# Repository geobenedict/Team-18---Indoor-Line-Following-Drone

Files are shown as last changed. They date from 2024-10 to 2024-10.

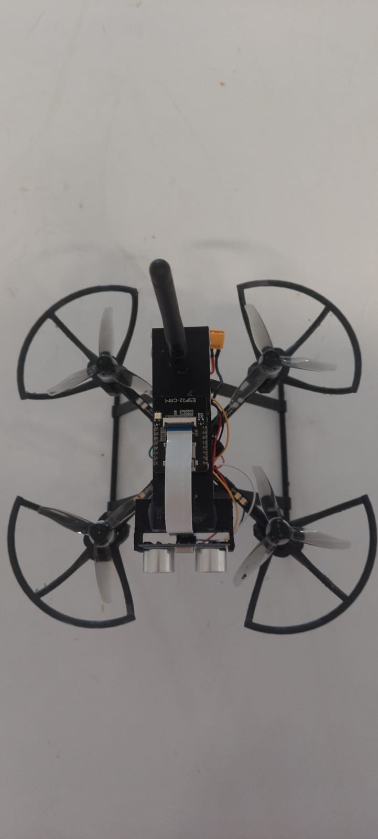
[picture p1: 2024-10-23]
Hardware-diagrams/Prototype Top View.jpeg

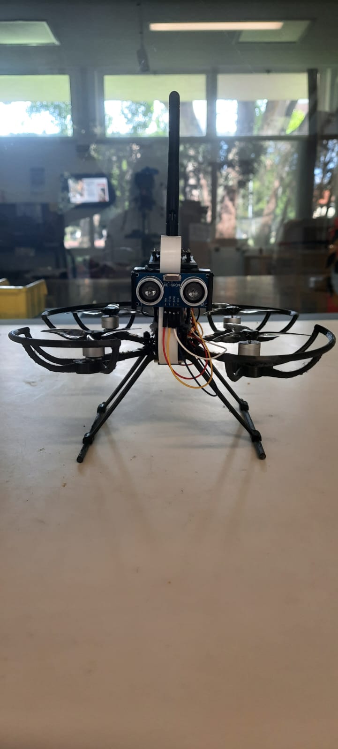
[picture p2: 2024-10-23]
Hardware-diagrams/Prototype Front View.jpeg

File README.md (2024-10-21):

# Team-18---Indoor-Line-Following-Drone

Welcome to the official repository for **Team 18's Indoor Line Following Drone Project**. This repository contains all the necessary files, including code, design deliverables, bills of materials, 3D print designs, and the design validation tests and results. The aim of this project is to develop a drone capable of autonomously following a predefined path indoors using a line-following navigation system.

## Project Overview

This project focuses on creating a lightweight, agile drone designed for indoor environments, equipped with a line-following system using the **ESP32-CAM** module and **OpenCV** for real-time image processing. The system captures live video, processes it to detect a line, and sends commands to control the drone's movements, ensuring it follows a predefined path.

### Key Features:
- Real-time video streaming via the **ESP32-CAM**.
- Line detection and navigation using **OpenCV**.
- Agile indoor navigation on the **Darwin FPV BabyApe Pro V2** platform.
- Design validation tests for line detection, curve navigation, and T-junction stopping.

## Repository Structure
📂 Team-18-Indoor-Line-Following-Drone ├── 📂 3d-Designs/ # 3D print designs for drone components ├── 📂 BoM/ # Bill of Materials (BoM) and expenses ├── 📂 Codes/ # Contains all the code for the ESP32-CAM and OpenCV integration  ├── 📂 Validation-tests/ # Design validation tests and results ├── 📂 Hardware-diagrams/ # Diagrams related to drone hardware and setup ├── 📄 README.md # Project overview and repository guide

## Getting Started

### Prerequisites

- **ESP32-CAM**: Ensure that the ESP32-CAM is set up using the Arduino IDE to act as an Access Point and stream video.
- **OpenCV**: Install   Pycharm to process the video feed and control the drone.
- **Arduino IDE**: Program the ESP32-CAM using the provided `.ino` code files in the `/Codes` folder.

### Installation

1. Clone the repository:
git clone https://github.com/geobenedict/Team-18---Indoor-Line-Following-Drone.git
2. Follow the instructions in the **/Codes** folder to upload the ESP32-CAM code via the Arduino IDE.
3. Use the Python code in the `/Codes` folder to set up the OpenCV environment for processing the video feed.

### Running the Project

1. Connect the **ESP32-CAM** to the drone and power it up.
2. Run the Python script from the `/Codes` folder to process the video stream and control the drone.
3. Validate the drone’s line-following performance by running the tests outlined in the **/Validation-tests** folder.

## Design Deliverables

- **3D Designs**: The `/3d-Designs` folder contains all the 3D print designs for custom drone components.
- **Bills of Materials**: All parts used in the project, along with their costs, are listed in the `/BoM` folder.
- **Hardware Diagrams**: Detailed hardware setup and wiring diagrams are located in the `/hardware-diagrams` folder.
- **Validation Tests and Results**: Test cases for straight-line, curve, and T-junction detection, along with their results, are found in the `/Validation-tests` folder.

## Design Validation

The design validation process included multiple tests, such as:
- **Straight Line Detection Test**: Ensures the drone follows a straight path.
- **Curved Path Detection Test**: Validates the drone’s ability to follow a curved line.
- **T-Junction Detection Test**: Confirms that the drone can detect a T-junction and stop as required.
- **Battery Drain Test**: Validates the efficiency of the battery's charge and discharge cycles by monitoring voltage levels, runtime, and overall power consumption under operational conditions.

Test results and detailed analysis are provided in the **/Validation-tests** folder.

**Team 18 - Indoor Line Following Drone Project**

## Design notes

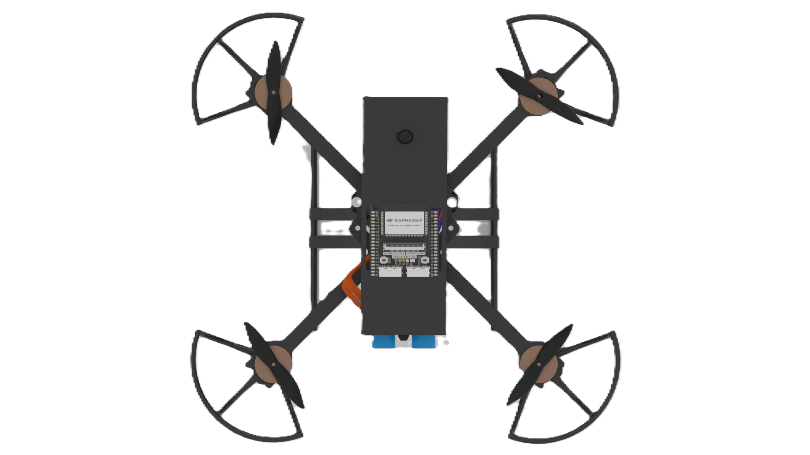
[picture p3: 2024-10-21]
Hardware-diagrams/Drone_top view.png

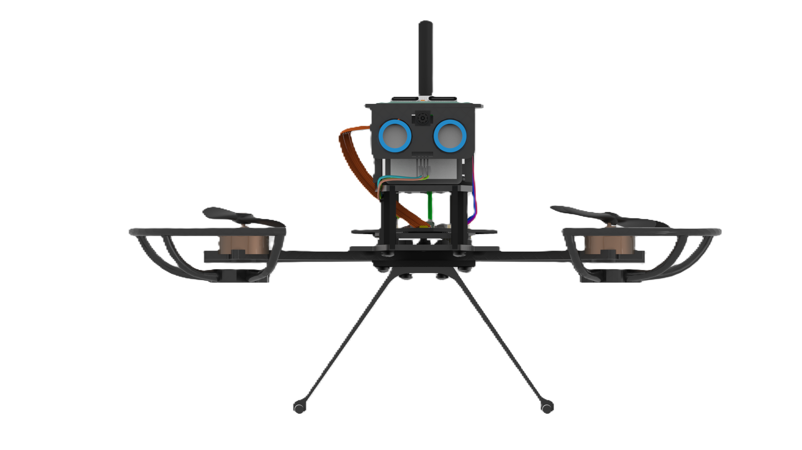
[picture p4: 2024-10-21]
Hardware-diagrams/drone front view.png

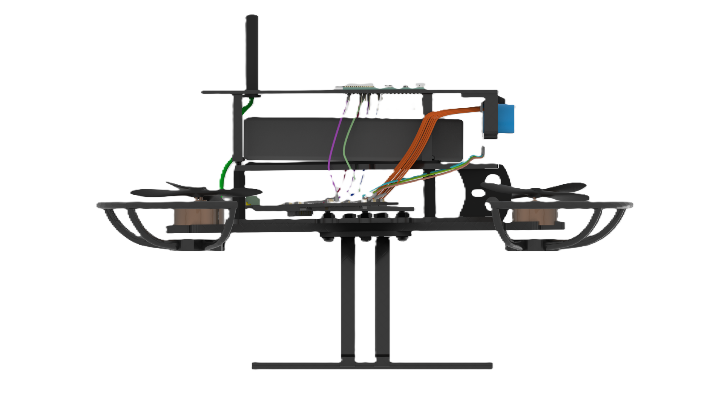
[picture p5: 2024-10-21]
Hardware-diagrams/Drone_side.png

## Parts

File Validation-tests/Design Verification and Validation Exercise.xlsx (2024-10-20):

Indoor Line Tracking Drone
ID | Requirement description | Test | Passed | Learnings
RQ1 | Follow the predefined path | Line Following Test: Use the ESP32-CAM to follow a predefined path (straight, curved, and T-junction) and verify correct navigation through image processing. Measure command accuracy for lateral and rotational adjustments. | Yes | The requirement was correctly tested, and the ESP32-CAM successfully followed the predefined path. However, variations in lighting conditions slightly impacted the accuracy of line detection. In future iterations, optimizing threshold values for varying lighting could enhance performance.
RQ2 | Battery Specifications | Battery Drain Test: Discharge the drone's battery fully while monitoring voltage levels and time taken. Record the total run time and compare against specifications. Perform a charging test to evaluate recharge time. | Yes | The battery drain and recharge process were successful, and no issues were observed with the battery specifications. Ensuring efficient power management and considering faster charging methods could further optimize drone operations.
RQ3 | Obstacle Detection | Sensor Obstacle Detection Test: Place obstacles at varying distances (20-50cm) and measure the response time of the ultrasonic sensor in triggering the hover or stop functions. Analyze detection accuracy and range. | Yes | The system successfully detected obstacles within 30cm. The sensor worked best within shorter distances, and future improvements could focus on increasing the detection range or adding more sensitive sensors for enhanced accuracy.
RQ4 | Project Deliverables | Documentation Review: Conduct a thorough review of all required project deliverables including the Bill of Materials (BOM), schematics, safety reports, and final project reports to ensure compliance. | Yes | All deliverables, including BOM and safety reports, were thoroughly reviewed with no discrepancies found. The project documentation is up to date ensuring compliance with the deliverables outlined in the project brief.
RQ5 | Fail-Safe Mechanisms | Emergency Stop Test: Simulate communication loss for over 30 seconds. Test the response of the manual emergency stop switch implemented using the ESP32 shield and verify if the drone halts all operations as expected. | No | The lack of integration between the hardware and software prevented full functionality. The system was not able to trigger the emergency stop during testing, and we could not test its behavior in a flight scenario. Integration challenges ultimately prevented a complete test of the fail-safe mechanism.
RQ6 | Safety Mechanisms - Propeller Shrouds | Motor and Propeller Guard Test: Run the motors at full speed with the propeller shrouds attached to verify that they effectively protect against damage and ensure safe operation in enclosed spaces. | Yes | The propeller guards performed as expected, protecting the motors and blades from potential damage. The design of the guards is effective for indoor navigation, but failed in testing with the drone in operation
RQ7 | Hovering and Stability | Drift Tolerance Test: Use the gyroscope and accelerometer to stabilize the drone in place. Measure the drift over a fixed duration while hovering and compare against drift tolerance limits (10cm drift allowed). | No | Stability was not fully tested due to the lack of software-hardware integration. Further testing will be needed once the drone can fly to ensure it remains within allowable drift limits. The stability features via sensors remain untested in a real-flight scenario.
RQ8 | Stable Altitude | Altitude Hold Test: Set the drone at various heights (1m, 1.5m, 2m) and assess the drone's ability to maintain stable altitude. Measure any fluctuations and calculate the stability at each height. | No | Stable altitude could not be tested as the drone was not operational. The flight controller and sensor integration are pending, which will be required for altitude testing once integration issues are resolved.
RQ9 | Open Source Software | Software Integration Test: Test the integration of the OpenCV libraries with the Arduino IDE for processing video feeds and executing commands. Ensure that the software correctly detects paths and sends commands to the drone. | Yes | Open-source libraries, including OpenCV and Arduino IDE, were successfully implemented, allowing for real-time video capture and processing. This was a cost-effective and flexible solution, reducing dependency on proprietary software and hardware platforms.
RQ10 | Budget Limit | BoM Review and Budget Test: Cross-check all components in the Bill of Materials (BoM) and ensure the total project cost does not exceed the $350 budget. Evaluate additional costs for any unforeseen expenses. | Yes | All components were purchased within the allocated budget of $350, with the current total reaching $300. The project remains within financial constraints, ensuring cost-efficiency.
RQ11 | Flight Range | Flight Duration and Range Test: Fully charge the drone's battery and run the drone to test the maximum flight range and duration. Measure the total distance covered on a full charge and ensure it meets the minimum range requirement. | No | Flight range could not be tested due to incomplete integration of the flight control system. This test will need to be conducted once the drone becomes operational to ensure that it meets the expected range requirements.
RQ12 | Collision Avoidance and Emergency Landing | Collision Avoidance Test: Simulate obstacles in the drone’s path. Test the ability of the system to detect obstacles using sensors and perform an emergency landing or hover. Record the time taken for the drone to stop or land. | No | Although the sensors were set up, collision avoidance and emergency landing could not be fully tested due to the incomplete integration of the flight system. These functionalities require proper sensor-drone interaction, which remains to be validated.
RQ13 | Product Quality | Durability Test: Monitor drone components (motors, sensors, propeller guards) over time by performing stress tests under normal and harsh conditions to assess long-term durability and consistent functionality. | Yes | Initial tests suggest that the components are durable and functional. However, extended monitoring is required to validate the long-term reliability of the hardware under normal operating conditions. The hardware components are currently performing as expected.
RQ14 | Communication via Base Station | Communication Stability Test: Set up the base station and ESP32 system. Test data transmission between the drone and base station over varying distances. Measure signal strength, latency, and data transfer consistency. | No | The communication between the drone and the base station could not be fully validated due to integration issues. Despite attempts to establish communication using the ESP32 module and antenna, reliable data transfer was not achieved. Future work will need to resolve these integration issues to ensure stable and continuous communication during operation.
RQ15 | Path Characteristics | Path Visibility Test: Assess the contrast and visibility of the path under different lighting conditions (e.g., bright and low light). Use the ESP32-CAM to verify the path’s detectability in various scenarios (floor type, path contrast). | Yes | Path detection worked well under various lighting conditions. The ESP32-CAM’s ability to distinguish the path was consistent, but fine-tuning is necessary to further improve contrast detection under extreme lighting differences.
RQ16 | Advanced Stabilizations | Betaflight Stabilization Test: Test the drone’s gyroscopes and accelerometers using Betaflight configurator. Verify if the drone stabilizes properly when external disturbances are applied during real-time flight simulation. | Yes | The gyroscopes and accelerometers were tested using the Betaflight configurator, and initial results indicated proper functionality for stabilization. However, full real-world testing could not be completed due to the lack of hardware-software integration, limiting the ability to verify stability during flight.
RQ17 | Battery Chargeability | Charging Test: Measure the time required to fully charge the battery using standard USB chargers. Record charging speed, temperature changes, and any indications of overcharging or overheating during the process. | Yes | The battery charging process worked effectively using standard USB chargers. Charging times were reasonable, and there were no issues with overheating or incorrect voltage. The charging process meets the project’s requirements and expectations.
RQ18 | Reliable Communication System | ESP32 Communication Range Test: Test the ESP32 module with external antennas to verify communication strength and reliability. Measure signal range and note any loss of connection or drop in data transmission as distance increases. | No | The integration of the ESP32 module with an external antenna was tested for enhancing communication range, but the system failed to provide reliable connectivity. Signal interference and loss of communication occurred at longer distances, highlighting the need for further refinement in antenna placement and communication protocols.
RQ19 | Size and Design Constraint | Dimensional Accuracy Test: Verify the dimensions of the drone to ensure it complies with size constraints for confined spaces. Ensure the frame and propeller guards allow safe navigation in tight spaces. | Yes | The drone’s size fits within the required constraints for indoor operations, ensuring it can navigate in tight and confined spaces. Further tests could confirm its suitability for environments with even more restricted dimensions.
RQ20 | Wi-Fi Coverage | Wi-Fi Strength Test: Use Wi-Fi signal strength tests to ensure data can be transmitted effectively over longer distances. Measure signal drop-off points and verify stability for continuous communication in a typical operational area. | Yes | Wi-Fi coverage was tested, and the signal strength was adequate for real-time data handling. The drone maintained stable communication over the tested distance, but further stress testing in environments with more interference would be beneficial for confirming robustness.

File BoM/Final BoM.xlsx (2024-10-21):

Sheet: BillOfMaterials
Bill Of Materials(BOM)
 | https://www.vertex42.com/ExcelTemplates/free-timesheet-template.html |  |  |  |  |  |  |  | © 2012-2019 Vertex42 LLC
 | Project Name : | Indoor Line Following Drone |  |  |  |  |  |  | Bill of Materials Template (https://www.vertex42.com/ExcelTemplates/bill-of-materials.html)
 | Assembly Revision : | 5 |  |  |  |  |  |  | ► More Inventory Templates (https://www.vertex42.com/ExcelTemplates/inventory.html)
 | Approval Date : |  |  |  |  |  |  |  | ► More Business Templates (https://www.vertex42.com/ExcelTemplates/business-templates.html)
 |  |  |  |  |  |  |  |  | ► More Spreadsheet Templates (https://www.vertex42.com/ExcelTemplates/)
 | Total Cost : | $349.27
Part # | Part Name | Description | Qty | Supplier | Unit Cost | Shipping charge | Tax | Total Cost
1 | Drone Kit | DarwinFPV BabyApe Pro V2 3 Inch Analog FPV Drone | 1 | FPV Faster | $145.87 |  | $14.59 | $160.46
2 | Battery | GAONENG GNB 720mAh 2S 100C 7.6V LiHV LiPo Battery Long Type XT30 [DG] | 1 | FPV Faster | $16.99 | $14.51 |  | $31.50
3 | Propeller | GEMFAN 3016 Hurricane Propeller Toothpick 3 Blade | 4 | FPV Faster | $3.99 |  |  | $3.99
4 | Battery Charger | MMOBIEL 2 Pcs USB Charger Cable LED Indicator Compatible with 800mA 2S 7.4V LiPo Batteries for RC Drones/Quadcopter/Vehicles with XH-3P Connector | 2 | Amazon | $11.49 |  |  | $11.49
5 | ESP 32 CAM | ESP32 Board with Cameras | 1 | Altronics | $32.95 |  |  | $32.95
6 | USB Programmer | Funduino USB programmer | 1 | Altronics | $19.95 |  |  | $19.95
7 | Ultrasonic sensor | Funduino Ultrasonic Sensor | 1 | Altronics | $7.95 |  |  | $7.95
8 | Antenna | Wi-Fi Antenna Dual Band RP-SMA with IPEX Cable | 1 | Lonely Binary | $6.99 | $9.95 |  | $16.94
9 | ESP 32 CAM Extension Cable | ESP32 Cam Extension Cable | 1 | Lonely Binary | $4.99 |  |  | $4.99
10 | 3D Printing | Charges of 3D printing | 8 |  | $50.00 |  |  | $50.00
11 | Other Accessories | Connecting Wires, double side tape, insulation etc. |  | Altronics | $9.05 |  |  | $9.05
 |  |  |  |  |  |  |  | $0.00
 |  |  |  |  |  |  |  | $0.00
 | Total |  | 21 |  |  |  |  | $349.27

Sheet: Revisions
Revision History
 | Assembly Name :
 | Assembly Number :
Revision | Revision Summary | Approval Date

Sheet: Example
Bill of Materials for LEGO® Design
 |  |  | https://www.vertex42.com/ExcelTemplates/free-timesheet-template.html |  |  |  |  |  |  | © 2012-2019 Vertex42 LLC
 |  |  | Assembly Name : | Mini X-Wing™ |  |  | [42] |  |  | Bill of Materials Template (https://www.vertex42.com/ExcelTemplates/bill-of-materials.html)
 |  |  | Assembly Number : | Custom
 |  |  | Assembly Revision :
 |  |  | Approval Date :
 |  |  | Pieces : | 46
 |  |  | Total Cost : | $5.85
Category | Part # | Elem ID | Part Name | Color | Qty | Units | Picture | Unit Cost | Cost
Bricks, Sloping | 50746 | 4504369 | ROOF TILE 1X1X2/3, ABS | 1 - White | 1 | each |  | $0.10 | $0.10
Plates | 3024 | 302401 | PLATE 1X1 | 1 - White | 1 | each |  | $0.10 | $0.10
Plates | 3023 | 302301 | PLATE 1X2 | 1 - White | 2 | each |  | $0.10 | $0.20
Plates | 3023 | 4211398 | PLATE 1X2 | 194 - Medium Stone Grey | 1 | each |  | $0.10 | $0.10
Plates | 3794 | 379401 | PLATE 1X2 W. 1 KNOB | 1 - White | 1 | each |  | $0.10 | $0.10
Plates | 3623 | 362301 | PLATE 1X3 | 1 - White | 1 | each |  | $0.10 | $0.10
Plates | 3623 | 362321 | PLATE 1X3 | 21 - Bright Red | 1 | each |  | $0.10 | $0.10
Plates | 94148 | 302201 | PLATE 2X2 | 1 - White | 1 | each |  | $0.15 | $0.15
Plates, Special | 6141 | 4210633 | PLATE 1X1 ROUND | 199 - Dark Stone Grey | 1 | each |  | $0.10 | $0.10
Plates, Special | 3070 | 307021 | FLAT TILE 1X1 | 21 - Bright Red | 4 | each |  | $0.10 | $0.40
Plates, Special | 2412 | 241201 | RADIATOR GRILLE 1X2 | 1 - White | 1 | each |  | $0.10 | $0.10
Plates, Special | 6019 | 4538353 | PLATE 1X1 W/HOLDER VERTICAL | 1 - White | 4 | each |  | $0.15 | $0.60
Plates, Special | 2431 | 4558168 | FLAT TILE 1X4 | 1 - White | 1 | each |  | $0.20 | $0.20
Plates, Special | 63868 | 4535737 | PLATE 2X1 W/HOLDER,VERTICAL | 1 - White | 4 | each |  | $0.15 | $0.60
Plates, Special | 2540 | 4211632 | PLATE 1X2 W. STICK | 194 - Medium Stone Grey | 4 | each |  | $0.15 | $0.60
Plates, Special | 3176 | 4225733 | COUPLING PLATE 2X2 | 199 - Dark Stone Grey | 1 | each |  | $0.20 | $0.20
Bricks, Special | 49668 | 4224793 | PLATE 1X1 W/TOOTH | 5 - Brick Yellow | 1 | each |  | $0.10 | $0.10
Technic | 32123 | 4211573 | 1/2 BUSH | 194 - Medium Stone Grey | 4 | each |  | $0.10 | $0.40
Technic | 6590 | 4211622 | BUSH FOR CROSS AXLE | 194 - Medium Stone Grey | 8 | each |  | $0.15 | $1.20
Accessories | 3957 | 4211473 | STICK/AERIAL | 194 - Medium Stone Grey | 4 | each |  | $0.10 | $0.40
 |  |  | Total |  | 46 |  |  |  | $5.85

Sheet: ©
Bill of Materials Template
By Vertex42.com
https://www.vertex42.com/ExcelTemplates/bill-of-materials.html
© 2012-2019 Vertex42 LLC
This spreadsheet, including all worksheets and associated content is a copyrighted work under the United States and other copyright laws.
Do not submit copies or modifications of this template to any website or online template gallery.
Please review the following license agreement to learn how you may or may not use this template. Thank you.
License Agreement
https://www.vertex42.com/licensing/EULA_privateuse.html
Do not delete this worksheet

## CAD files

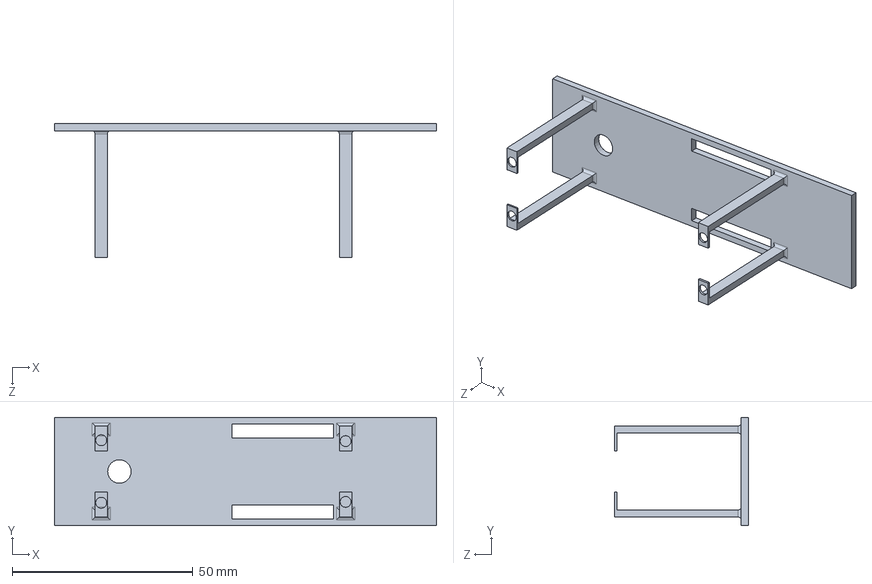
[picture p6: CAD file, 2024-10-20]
3d-Designs/ESP32 CAM Plate.SLDPRT
105.8 x 30.0 x 37.0 mm

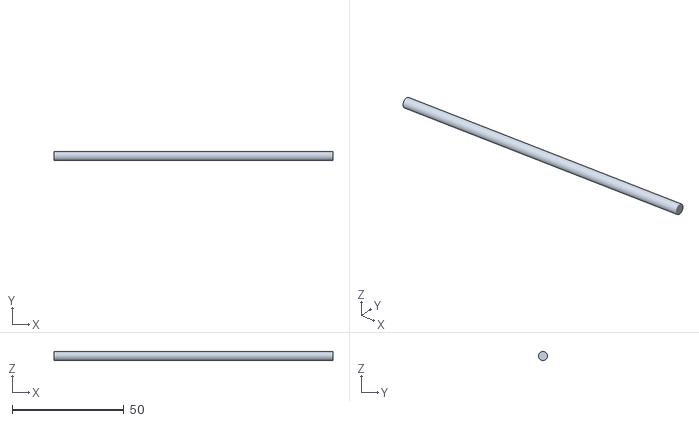
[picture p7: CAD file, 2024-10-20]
3d-Designs/Landing Gear/darwin_landing_gear_-_Part_2.stl
125.0 x 4.09 x 4.10

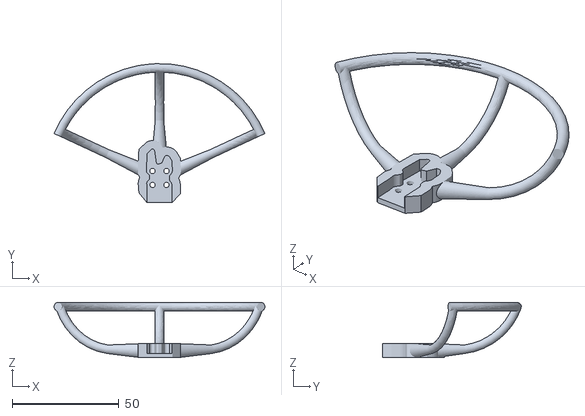
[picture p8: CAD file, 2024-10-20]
3d-Designs/Baby_Ape_2_Prop_Guard.stl
98.7 x 64.9 x 25.8

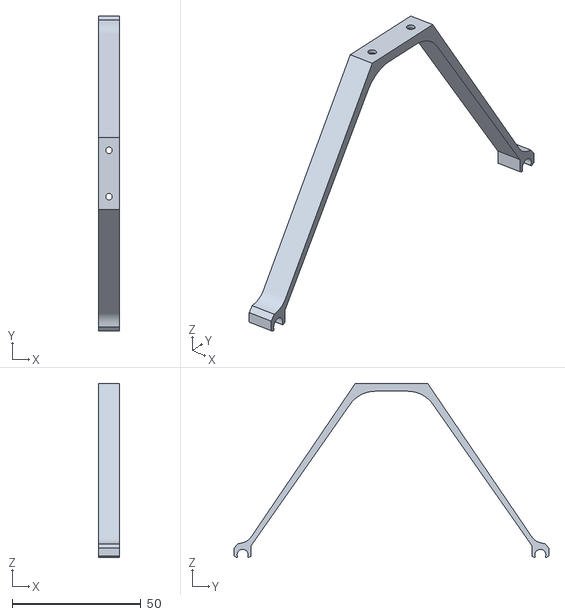
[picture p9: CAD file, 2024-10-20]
3d-Designs/Landing Gear/darwin_landing_gear_-_Part_1.stl
8.00 x 122.0 x 67.5

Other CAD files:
3d-Designs/Landing Gear/darwin_landing_gear_-_Part_4.stl
3d-Designs/Landing Gear/darwin_landing_gear_-_Part_3.stl

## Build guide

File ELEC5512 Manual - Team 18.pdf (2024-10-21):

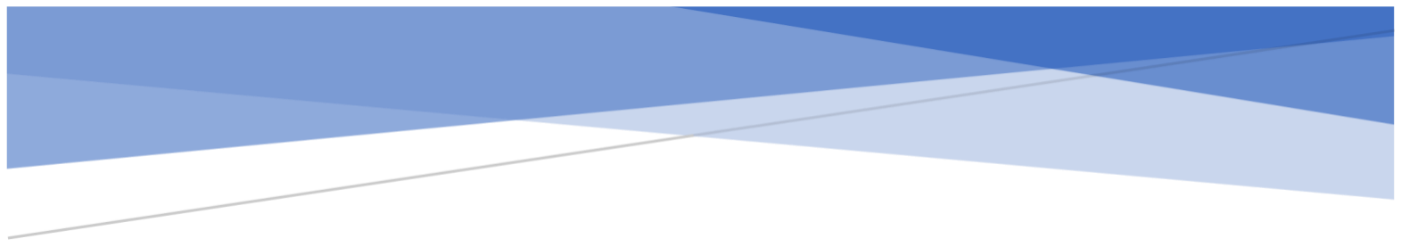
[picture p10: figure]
INDOOR LINE FOLLOWING DRONE

## Prototype Design and User Manual Indoor Line Following Drone

## Table of Contents

List of Figures
Figure 1: Assembled (a) bottom plate (b) top plate (c) arms (d) battery strap | 7
Figure 2: F411-AIO FC | 8
Figure 3: 1104 4300KV Motor | 9
Figure 4: Gemfan 3016 Propeller | 11
Figure 5: Mounting plate design sketch (NB: All the measurements are in ‘mm’) | 12
Figure 6: Final sketch with extrusion | 13
Figure 7: Rendered Model | 13
Figure 8: Insert the ESP32-CAM module to the top plate | 14
Figure 9: Mounting plate secured on to the top plate of the drone | 14
Figure 10: Mount for Ultrasonic Sensor (HC-SR04) | 15
Figure 11: Ultrasonic sensor holder with the ESP32-Cam mounting plate | 15
Figure 12: 3D print model for Propeller guard | 15
Figure 13: Printed Propeller guards | 16
Figure 14: Landing Gear | 16
Figure 15: Drone Prototype Front View | 17
Figure 16: Side View | 17
Figure 17: Top View | 18
Figure 18: Pycharm download window | 19
Figure 19: Pycharm welcome page | 19
Figure 20: Python download window | 20
Figure 21: Pycharm Terminal | 20
Figure 22: Run icon in Pycharm | 21
Figure 23: Output | 22
Figure 24: Ultrasonic sensor wiring diagram | 22
Figure 25: Ultrasonic sensor wiring diagram for uploading the code | 23
Figure 26: Wi-Fi connection using ESP32-CAM | 24
Figure 27: User id and password | 24
Figure 28: IP address camera feed | 25
Figure 29: external and on-board antenna solder connection | 26
Figure 30: Basic design overview | 26

List of Tables
Table 1: Drone specifications | 5
Table 2: Electronics Components List | 5
Table 3: Mechanical Component List | 5
Table 4: Accessories List | 6

1. Introduction

The manual is designed to provide comprehensive guidance on the design, assembly , setup and operation of the indoor line following drone, developed from Darwin Baby Ape 3” drone, which is exclusively built for autonomous remote safety inspections of the Australian National Fabrication Facility(ANFF) laboratory.

The drone model is developed from Darwin Baby Ape pro-3” toothpick drone kit which is equipped with advanced features like AIO-FC. The prototype is built to meet the specific requirements as stated by the stakeholders.

The methods and techniques outlined in the drone is specifically tailored to the upgraded version of Darwin Baby Ape Pro 3” drone, configured for line-following specifications. This manual only provides the basic setup and operational guidelines required to build and test the drone.

While the system encountered limitations in achieving a successful flight during testing, the approaches described here can serve as a foundation for further research and improvisations. The information presented is intended to assist in the refinement of the current prototype and to inspire future enhancements in drone design and functionality.

2. Product Specifications

Table 1: Drone specifications

Drone Kit used | Darwin BabyApe Pro V2 FPV Drone
Frame structure | 3-inch toothpick frame
Flight Controller | F411-AIO FC
Motor | 1104 4300KV 2-3S Brushless Motor
Recommend Battery | 1S-2S LiPo battery
Propeller | Gem fan 3016 propeller
Battery | GNB 720mAh, 2S 100C battery
Flight time | 7 mins
Camera and Microcontroller | ESP32-Cam
Object Detection | Up to 30 cm
Charger | MMOBIEL USB Charger Cable
Weight | 130 g

Table 2: Electronics Components List

No | Description | Specification | Qty
01 | Flight Controller | F411-AIO FC | 1
02 | ESP32-Cam | ESP32 Wi-Fi-Bluetooth Camera Module Development Board | 1
03 | Camera | OV2640 Camera Module | 1
04 | Ultrasonic Sensor | HC-SR04 | 1
05 | External RF Antenna | RF Dual Band RP-SMA Antenna | 1
06 | Battery | GNB 720mAh, 2S 100C battery | 1
07 | Receiver | ELRS Re1ceiver | 1

Table 3: Mechanical Component List

No | Description | Specification | Qty
01 | BLDC Motor | 1104 4300KV Motor | 4
02 | Propeller | Gem fan 3016 Propeller | 1
03 | Screw | M1 4*5 | 20
04 | Screw | M2*4 | 5
05 | Screw | M2*6 | 10
06 | Screw | M2*8 | 5

07 | Screw | M2*10 | 5
08 | Screw | M2*12 | 5
09 | Nuts | M2 nylon nuts | 15
10 | Nuts | M2 Iron nuts | 5
11 | Pads | M2*1mm*0.5mm | 5
12 | Columns | M2*15 | 5

Table 4: Accessories List

No | Description | Specification | Qty
01 | ESP32-CAM mount plate | 3D printed model for mount plate | 1
02 | Propeller Guard | 3D printed propeller shrouds | 4
03 | Landing Gear | 3D printed landing gear | 1
04 | Ultrasonic Sensor Holder | 3D printed model -Ultrasonic Sensor holder | 1
05 | Jumper Wire | Connecting wires | 1 pack
06 | Adhesives | Hot glue gun, double sided tape | 1 each

3. Part 1- Hardware Integration

### 3.1 Frame Built

The Drone kit comes with a 3” frame consisting of top, mid plate and bottom plate along with crush plate and a battery strap. All the frame plates are to be assembled using the mechanical components starting from No 3 as listed in table 3. The top, bottom, mid and the assembled figure is shown below:

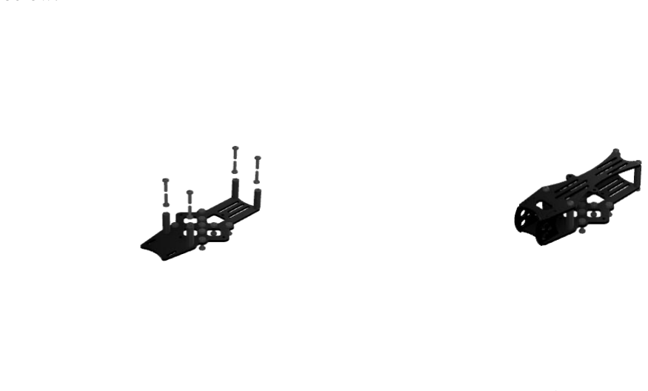
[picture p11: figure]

(a) (b)
(c) (d)

Figure 1: Assembled (a) bottom plate (b) top plate (c) arms (d) battery strap

### 3.2 Drone Control Unit

The drone control Unit consists of an F411-AIO Flight Controller along with an STM32F411CEU6 microcontroller as the main processing unit.

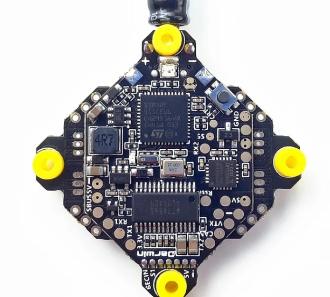
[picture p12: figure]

Figure 2: F411-AIO FC

The key features and instructions for usage are detailed below:
1. Overview and Key Features:
- Processor: The FC is integrated with an STM32 F411 microcontroller that enables efficient data processing in real time.
- A built-in 6-axis gyroscope and accelerometer that helps in real-time stabilization thus enabling stable flight.
- Input Voltage: 3.7 V
- Constant current: 15 A
2. Power & Connectivity
- Power Distribution: Supports 1S to 4S LiPo batteries
- ESC Compatibility: Supports both BLHeli_S and DShot protocols thus enabling smooth and efficient motor control.
- Receiver Compatibility: Supports SBUS, IBUS, DSMX, and other popular radio receiver protocols.
3. Setup & Configuration
- FC F411-AIO is configured using Betaflight Configurator. This allows firmware updates, fine-tuning flight parameters, and monitoring sensor performance.
- The Betaflight firmware is flash-updated to the flight controller using a USB cable.
- The FC is flashed by altering the setting in the Betaflight configurator
- The blinking of the LEDs indicates that the FC is flashed.
- The FC can also be flashed by connecting the battery thrice and then finally connecting the battery completely to the system.
- The FC also enables PID tuning to optimize the drone’s response.
4. Installation
- The F411-AIO is compactable and perfectly fits inside the drone.
- It is mounted to the frame using screws

- The flight controller is then wired to the motors, ESC, and other components depending upon the wiring diagram.
5. Maintenance

The FC must be handled with care to avoid damage and to ensure maximum performance.
- The FC should be properly ventilated to avoid overheating during operation.
- The FC must be updated periodically to have access to the latest features and to have maximum performance efficiency.
- The FC must be properly secured to the frame to protect it from any physical damage in case of any crash landings.

### 3.3 Motor and Propeller

The propulsion system includes a set of four motors along with four propellers.

3.3.1 Motor

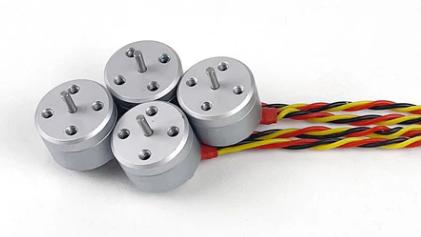
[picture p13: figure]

Figure 3: 1104 4300KV Motor

The motor used in the drone kit has the following specifications:

1. Overview of the motor:
- Model: 1104 4300kV Brushless Motor
- Application: Mainly designed for small, compact light weighted drones like toothpick drones and micro-quads
- Suitable Battery: Mostly used along with 1S or 2S LiPo batteries. Can be used with 3S batteries only if proper cooling techniques are provided. Ideal for 2S batteries.
- KV Rating: The rating of the motor used is 4300kV which means that the motor can have 4300 revolutions per minute per volt
- Motor Type: The motor type is a Brushless DC motor which provides higher efficiency, they are long-lasting and provides better performance compared to brushed motors.
2. Technical Specifications of the motor:
- kV Rating: 4300kV (kV = RPV per volt)
- Configuration of the motor: 9N12P which means the motor has 9 stator poles and 12 magnets present in it)
- The weight of the motor is approximately around 5-7 grams per motor.

- The diameter of the shaft is 1.5mm
- The mounting pattern consists of 4 x M2 screws with 9mm hole spacing provided in it.
- The dimensions of the motor are 14.3mm x 17.6mm
- The diameter of the stator is about 11mm, and the height of the stator is 4 mm.
- The maximum continuous current is 5.2 A
- The maximum power consumed is 62.4 W
- A 3-inch propeller (GEMFAN 3016-3) is used for proper balancing and sufficient flight time
- The high-quality bearings of dimension ɸ 4 x ɸ1.5 x 2mm
3. Battery Compatibility :
- The motor is compatible with 1S to 2S LiPo batteries.
- Mostly a 2S battery is recommended
- The operating voltage of the selected battery is 7.6 V(nominal)
4. Performance Data
- The performance of the motor depends on the propeller selected and the throttle levels at which the motor is run.
- At 100% throttle for a 2S battery at 7.6 V using a 3-inch propeller is about 97.533g.
5. Wiring Information
- The wires used in the motor have different color coding, the black wire used act as ground, red wire as a positive connection where power is input and the yellow wire is the signal wire.
6. Mounting of the motor
- The M2 screws are used to secure the motor to the frame. The screws used are small to prevent any further damage to the motor windings.
- The motor should be properly installed, and the propeller should be attached in the right direction (clockwise or counter-clockwise ) for optimal lift.
7. Maintenance
- The motors must be kept clean and free from dust, dirt, and moisture
- The bearings must be lubricated frequently
- Make sure that the motors are provided with sufficient ventilation to avoid overheating.
8. Cautions and Safety Warnings
- Avoid running the motor at full throttle for long hours without proper ventilation to prevent the motor from getting damaged.
- Use a battery monitoring system or alarm to prevent over-discharging of the batteries
- The motor efficiency can be varied by varying the throttle at which the motor should run. The selection of the proper throttle level helps in extending the life of the battery.
- Make sure that the propellers are tightly and properly mounted to the motors to avoid vibrations that can damage the motor.

9. Troubleshooting
- In the case of motor stuttering, check if there are any loose connections or try recalibrating the ESC
- When the motor is not spinning in that case check for any loose connections, or short circuits and check for the ESC programming.
- In case of overheating, check whether the motor is running above its rated voltage.

### 3.3.2 Propeller

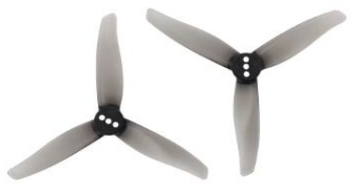
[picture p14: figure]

Figure 4: Gem fan 3016 Propeller

1. Overview and Specifications
- GEMFAN 3016-3 is the model’s name of the propeller used
- A 3 blade 3-inch propeller
- Made up of durable polycarbonate
- Used mainly in micro drones for high efficiency and responsive control
- The pitch size is 1.6 inches
- The center hole inner diameter is 1.5 mm
- The total weight of the propellers is 1.18g
2. Performance
- The propellers help in providing a balanced thrust and efficient performance with 2S batteries.
- Works best with 1104 4300KV motors to deliver maximum thrust.
3. Installation
- The propeller blades should be properly mounted to ensure optimal lift.
- There are 2 sets of clockwise propellers rated as 3016 and 2 sets of counterclockwise propellers rated as 3016R.
- The 3016R propeller must be mounted to the motor shaft rotating in the counterclockwise direction and vice versa.
4. Safety and Maintenance

- The propellers must be durable to withstand any damage from crash landings.
- The propellers must be guarded using a propeller guard to protect the propeller and to provide safety.
4. ESP32-CAM Mount Plate Design

The section provides the detailed overview of the custom-designed mount for integrating the ESP32-CAM onto the drone, specifically for implementing line-following and obstacle detection functionality. The mount is designed to be securely attached to the drone’s top plate, positioned above the battery strap, ensuring stable placement without interfering with other components. All design work and renderings were carried out using Autodesk Fusion 360 (Education License Version), ensuring precision and adaptability to the drone’s structural requirements.

4.1 Drawings

The initial step in designing the mounting plate is to take the precise measurements of the drone’s top plate. While the primary dimensions were based on the top plate, the length of the mounting plate is intentionally extended beyond the top plate’s size to provide additional spacing for holding the antenna securely.

The ESP32-Cam used in the project is a development board equipped with header pins on the bottom side. To make connections with the flight controller using jumper wires, rectangular cutouts are made on both sides of the plate. The cutouts facilitate the insertion of the header pins, ensuring clean and secure connection.

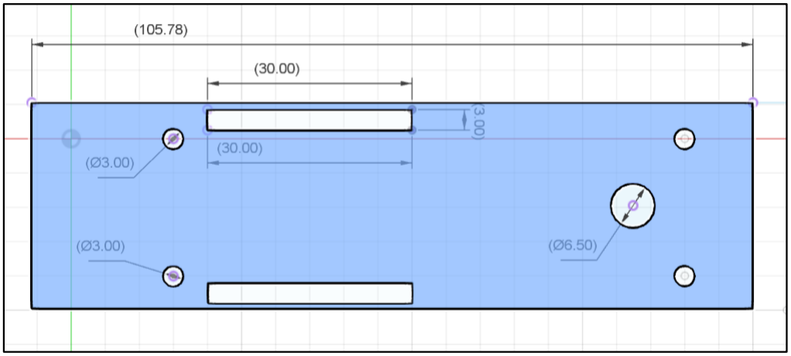
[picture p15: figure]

Figure 5: Mounting plate design sketch (NB: All the measurements are in ‘mm’)

The sketch is extruded with a thickness of 2mm providing sufficient strength without adding excess weight. Furthermore, four cylindrical columns are provided to the bottom of the mount, aligning with the screw positions on the drone’s top plate. These columns allow the plate to the securely placed without impacting the drone’s aerodynamics, ensuring stability during operation.

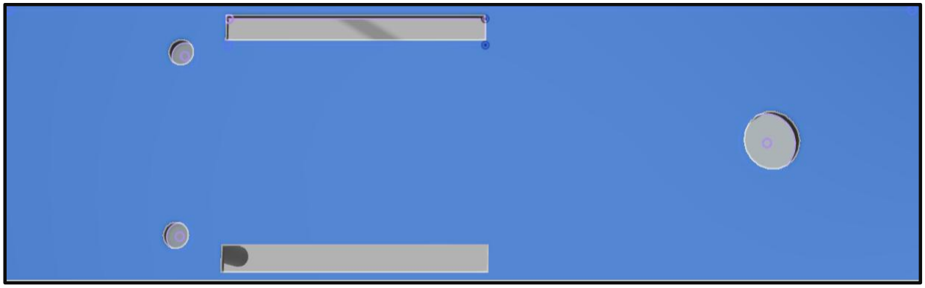
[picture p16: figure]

Figure 6: Final sketch with extrusion

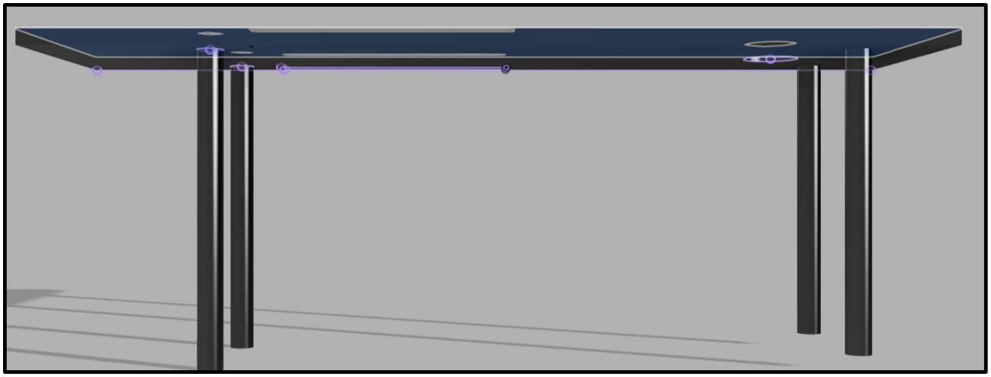
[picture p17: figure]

Figure 7: Rendered Model

The model file is converted into .STL format and is 3D printed after slicing it using Cura (open-source slicing software developed by Ulti maker) and converting it into G-code format. The 3D printing material used is PLA black with the print temperature around 180 degrees Celsius.

4.2 Alignment
The ESP32-Cam header pins are to be inserted through the rectangular cutout within the 3D printed model. Jumper wires are connected through the header pins to the flight controller. It is to be noted that, to tightly stick the ESP32-CAM onto the plate, adhesives such as doble-sided tape can be applied underneath the module.

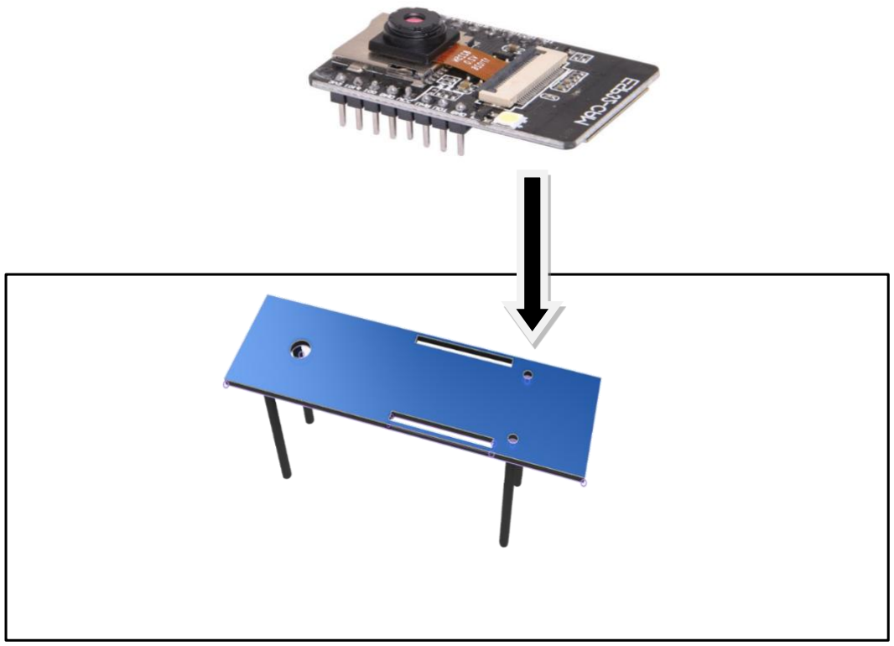
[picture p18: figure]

Figure 8: Insert the ESP32-CAM module to the top plate

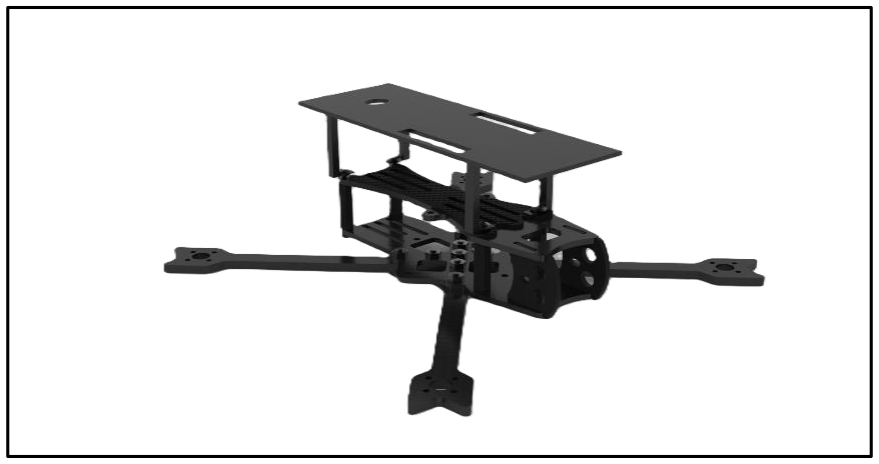
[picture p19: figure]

Figure 9: Mounting plate secured on to the top plate of the drone

The final assembled module on to the top of the drone is shown in figure 5. The plate is stuck on to the top plate using hot glue gun. It is important to note that hot glue gun may not provide sufficient hold for a drone flying at high speeds and it could potentially damage the module in the event of a crash. Therefore, alternate methods should be explored for securely integrating the mounting plate to the drone, ensuring both stability and safety.

4.3 Ultrasonic Sensor Holder Design

The ultrasonic sensor mounted onto the drone using a holder obtained from an online design repository . The holder is 3D printed using the black PLA material for durability and lightweight properties. It is securely glued to the bottom position of the ESP32-CAM mounting plate ensuring a stable and effective setup for obstacle detection.

Figure 10: Mount for Ultrasonic Sensor (HC-SR04) | Figure 11: Ultrasonic sensor holder with the ESP32-Cam mounting plate

As previously indicated for ESP32-Cam mount plate, it important to note that hot glue gun may not provide sufficient hold for a drone flying at high speeds and it could potentially damage the module in the event of a crash, so care must be taken during the flight operation. For future improvements, screw holes can be provided in the holder, so that it can be screwed to the bottom plate of the drone, but this can affect the aerodynamics of the overall system which might affect the stability of the drone during flight.

4.4 Propeller Guard Design

The propeller guards are 3D printed from files obtained from an online repository []. Four propeller guards, created using PLA Black material, are affixed to the arms of the drone. Prior to installation, the printed components require some filing to ensure proper fit to the arms.

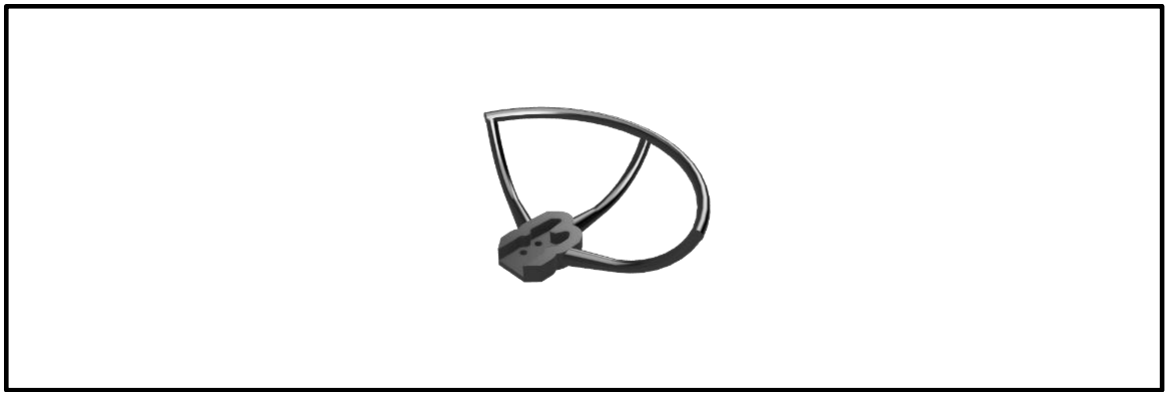
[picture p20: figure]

Figure 12: 3D print model for Propeller guard

However caution must be taken to avoid excessive filing as this could result in a loose fit and compromise the intended functionality of the propeller guards. To enhance the security of the installation, hot glue is applied to further secure the propeller guards to the drone.

Figure 13: Printed Propeller guards

4.5 Landing Gear Design

The landing gears are 3D printed from files obtained from an online repository. To prevent the damage of critical components of the drone landing gears are crucial. The files are in 4 different parts and printed separately. Once printed, these are then attached together. The ‘V’ shaped bars are fixed to the bottom plate of the drone using some screws. This might lead to some stability issue during flight. Due to the unsuccessful flight attempts, it is unable to fully comprehend the operational dynamics of the drone. Once the issues with the flight controller commands are resolved, it will be essential to assess the stability of the drone during subsequent test flights.

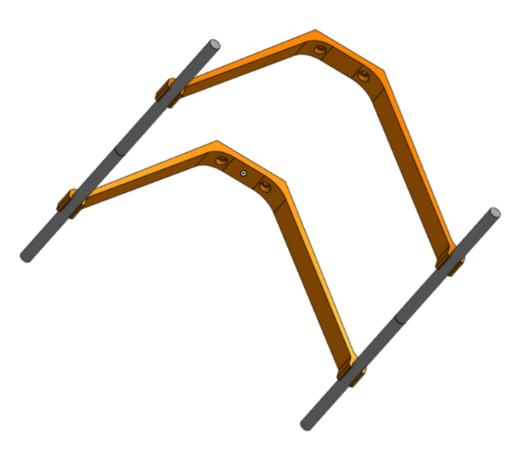
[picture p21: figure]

Figure 14: Landing Gear

4.6 Final Design

The final product for the end user is illustrated in the figure below. A comprehensive step-by-step guide for its operation is provided in the subsequent sections.

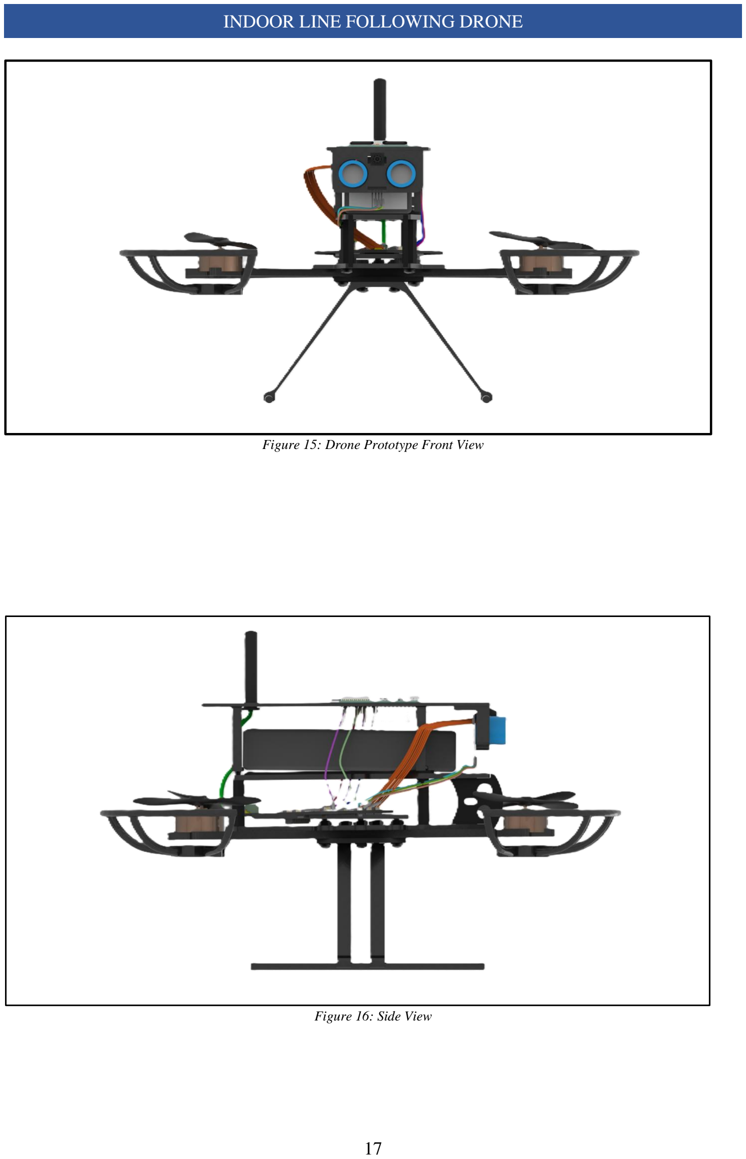
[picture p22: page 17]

Figure 15: Drone Prototype Front View

Figure 16: Side View

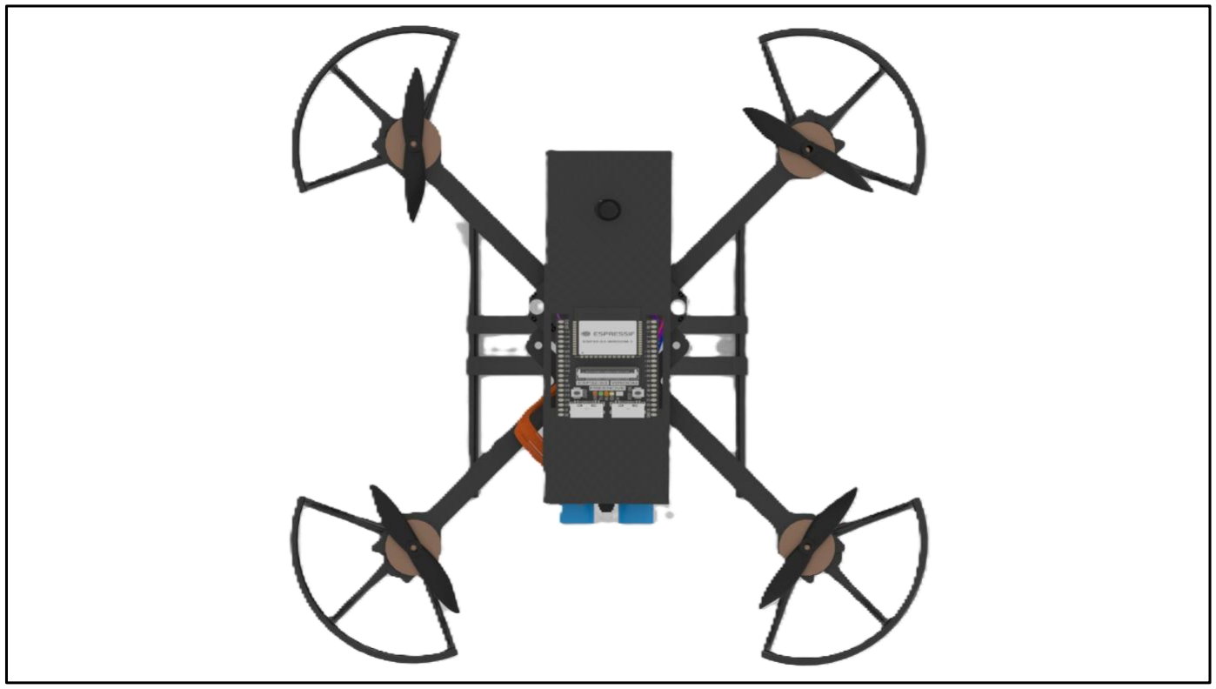
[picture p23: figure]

Figure 17: Top View

NB: The figure above shows 2-blade propeller; however the system uses a 3-blade propeller.

5. Part 2- Software Integration

5.1 Setting up Pycharm IDE
This section provides step-by-step instructions for installing PyCharm, setting up the necessary environment, and running the code for the drone line-following project using OpenCV and ESP32-CAM.
Step 1: Install Pycharm
Pycharm is an Integrated Development Environment (IDE) used to write and run Python code.

5.1.1 Download Pycharm:
- Go to the official PyCharm website: https://www.jetbrains.com/pycharm/download
- Download the Community version

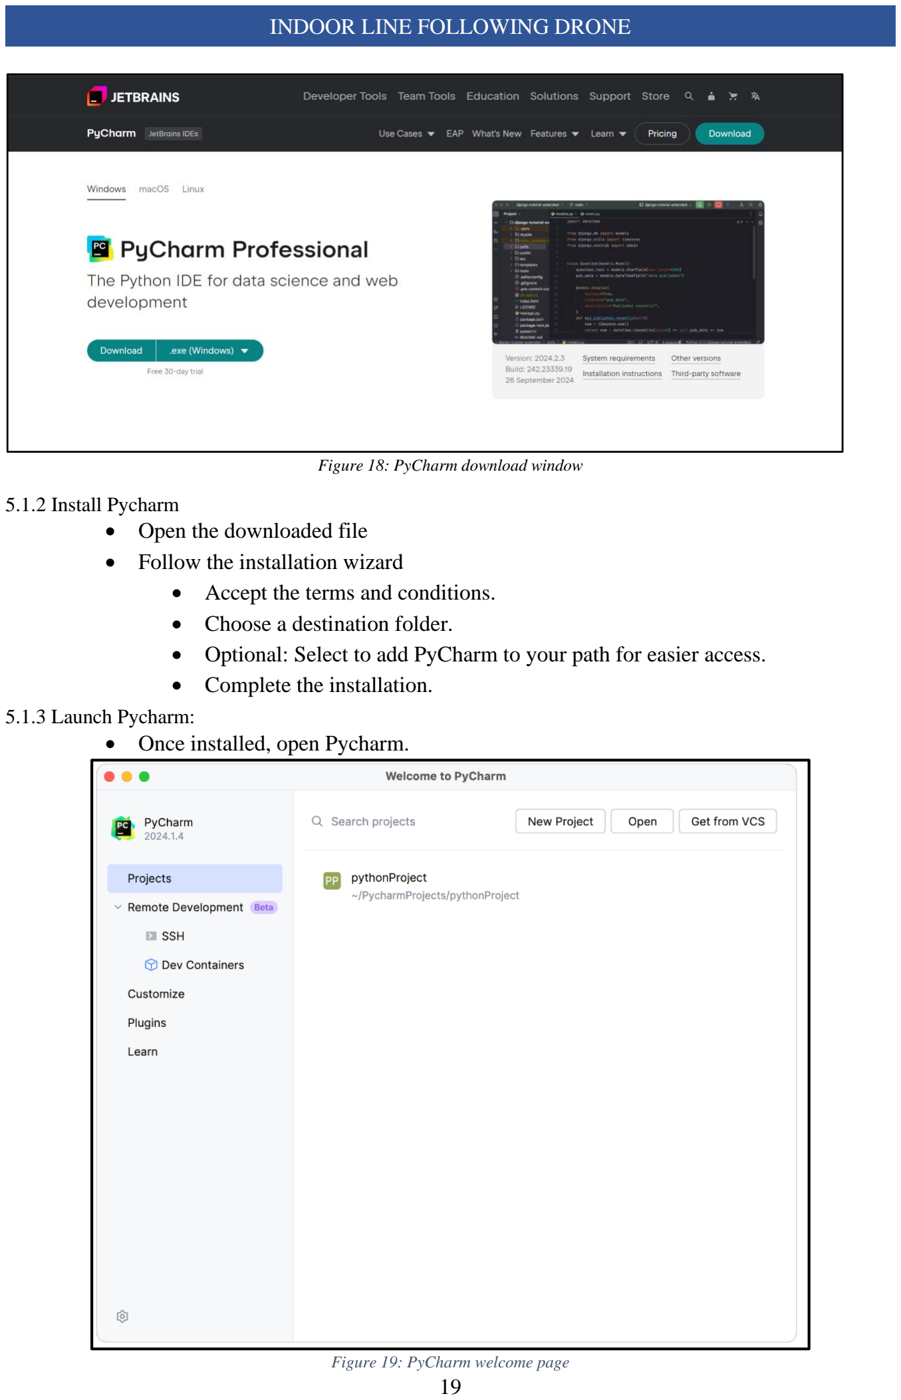
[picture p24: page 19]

Figure 18: PyCharm download window

5.1.2 Install Pycharm
- Open the downloaded file
- Follow the installation wizard
- Accept the terms and conditions.
- Choose a destination folder.
- Optional: Select to add PyCharm to your path for easier access.
- Complete the installation.

5.1.3 Launch Pycharm:
- Once installed, open Pycharm.

Figure 19: PyCharm welcome page

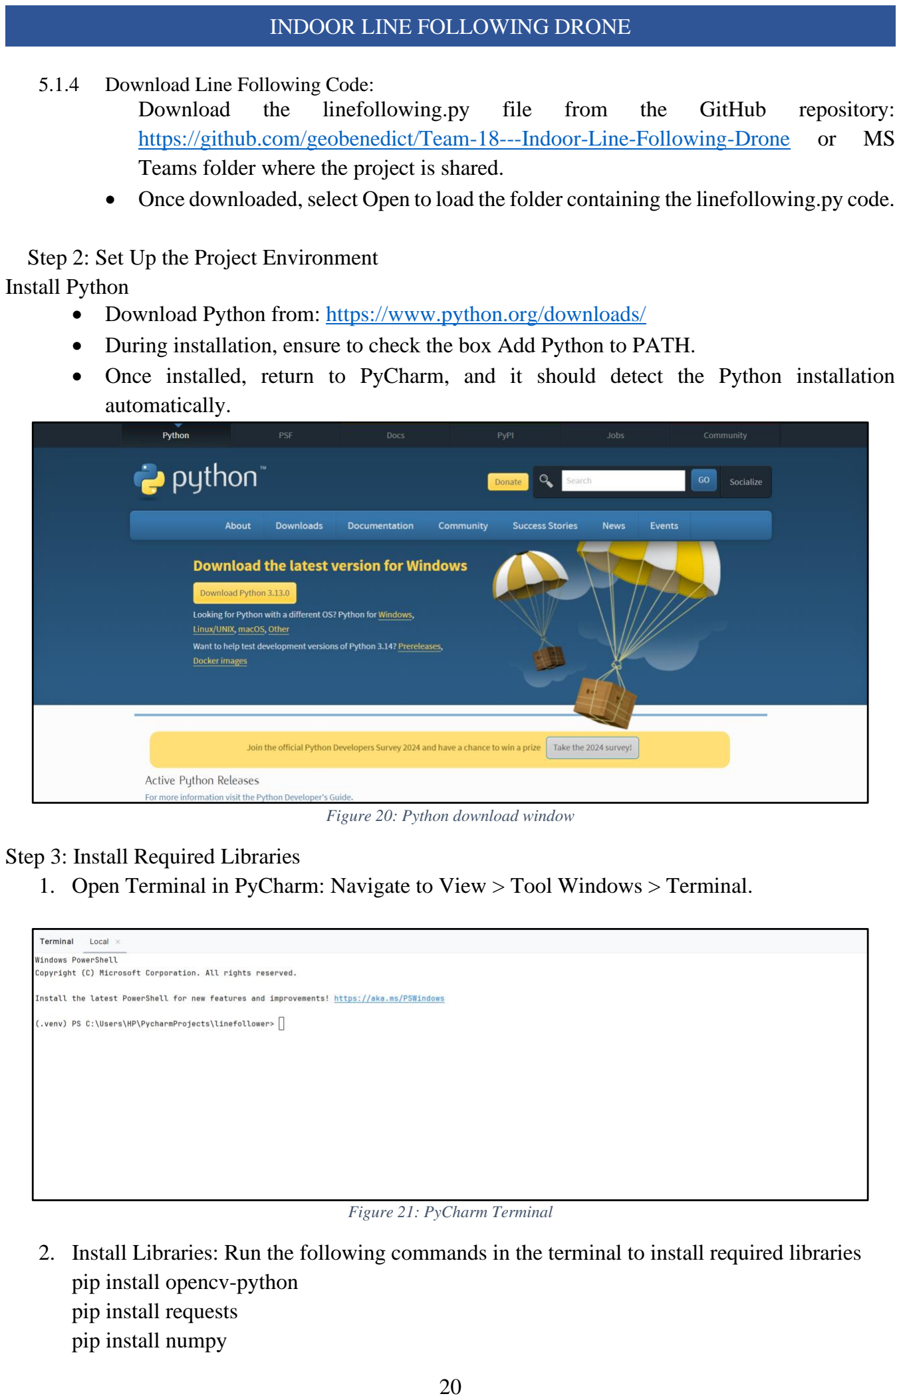
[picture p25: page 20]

5.1.4 | Download Line Following Code:
Download | the | linefollowing.py | file | from | the | GitHub | repository:
https://github.com/geobenedict/Team-18---Indoor-Line-Following-Drone | or | MS
Teams folder where the project is shared.
- Once downloaded, select Open to load the folder containing the linefollowing.py code.
Step 2: Set Up the Project Environment
Install Python
- Download Python from: https://www.python.org/downloads/
- During installation, ensure to check the box Add Python to PATH.
- Once installed, return to PyCharm, and it should detect the Python installation automatically.

Figure 20: Python download window

Step 3: Install Required Libraries
1. Open Terminal in PyCharm: Navigate to View > Tool Windows > Terminal.

Figure 21: PyCharm Terminal

2. Install Libraries: Run the following commands in the terminal to install required libraries pip install opencv-python
pip install requests
pip install numpy

Step 4: Run the Code
1. Connect to ESP32-CAM:
Ensure that your ESP32-CAM is connected and set up as an access point, streaming video to your computer.
- Follow the instructions in the ESP32-CAM setup section
2. Configure the IP Address in the Code:
- Inside the code, locate the line where the IP address of the ESP32-CAM is specified. It might look like:
url = 'http://192.168.4.1/capture'
- Ensure the IP matches the one generated by your ESP32-CAM. Modify it if needed.
3. Run the Code:
- In PyCharm, locate the Run option at the top of the interface or right-click on the main code file and select Run.

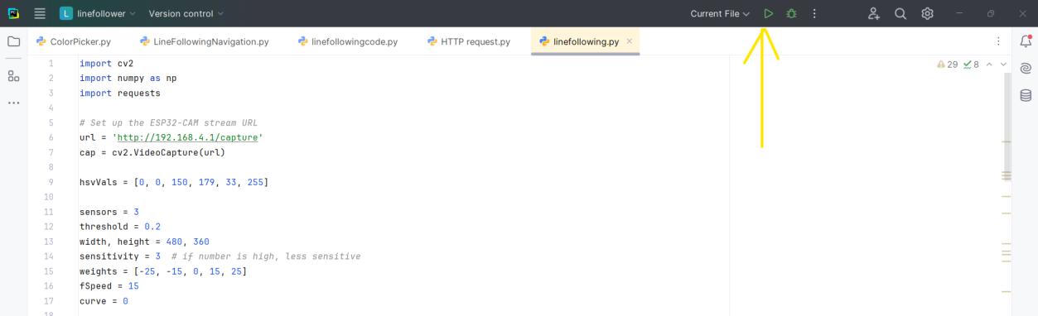
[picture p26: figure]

Figure 22: Run icon in PyCharm

- The program will begin to execute, capturing the video stream from the ESP32-CAM and processing it to detect the line.
Step 5: Viewing the Results
1. Console Outputs:
- While the program is running, observe the console output in PyCharm.
- You should see information about the drone’s movement commands (e.g., forward speed, rotational adjustments).
2. Graphical Output:
- A window should open displaying the real-time video stream from the ESP32-CAM, with overlays showing detected lines and any adjustments being made to the drone’s path.

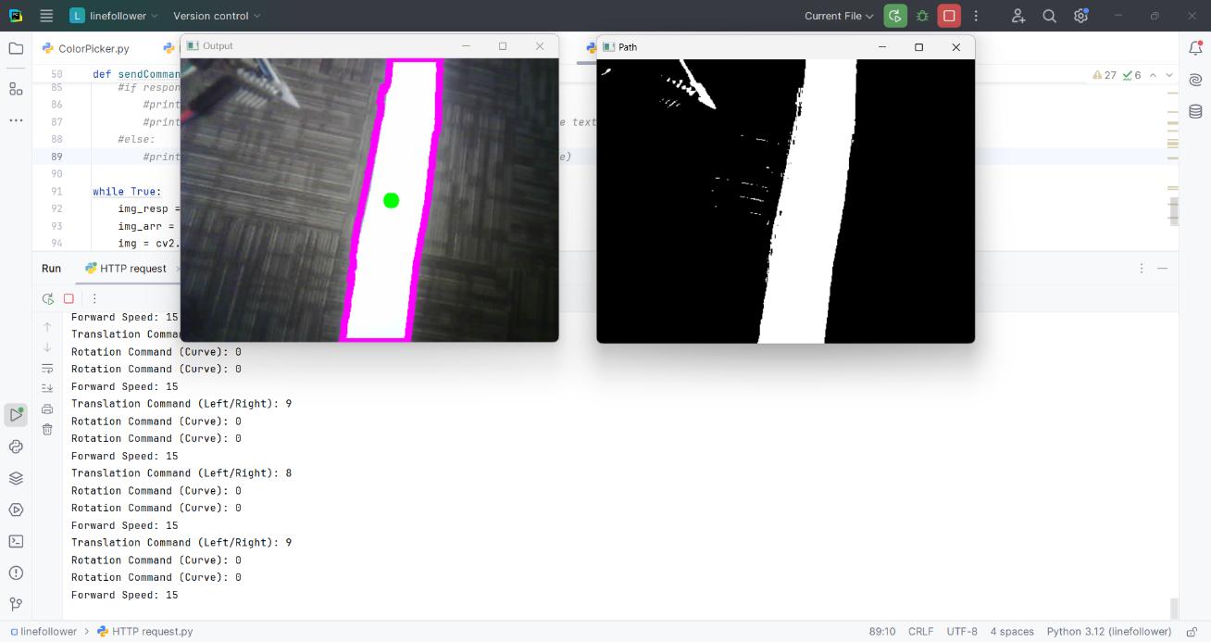
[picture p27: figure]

Figure 23: Output

Step 6: Troubleshooting
1. No Video Feed:
- Ensure the ESP32-CAM is properly set up and connected to your local network.
- Double-check the IP address in the code and confirm the ESP32-CAM is streaming.
2. Missing Libraries:
- If you encounter missing library errors, return to Step 3 and ensure all necessary Python libraries are installed.

5.2 Ultrasonic Obstacle Detection

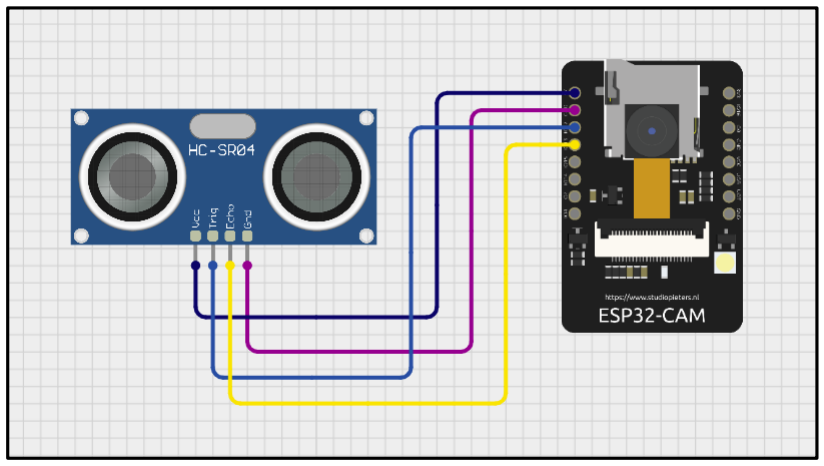
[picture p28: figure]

Figure 24: Ultrasonic sensor wiring diagram

Steps to view the results in the serial monitor

Setup and Connect the Hardware:

### 1. Ensure the ESP32 CAM and ultrasonic sensor are properly connected as per the wiring

diagram.
2. Connect the ESP32 CAM to your computer via FTDI for flashing and monitoring.

Open the Arduino IDE:

1. Open the Arduino IDE on your computer.
2. Ensure the necessary board drivers for ESP32 are installed. If not, go to File > Preferences
and | add | the | following | URL | to | the | additional | board | manager | URLs:
https://dl.espressif.com/dl/package_esp32_index.json
3. Then go to Tools > Board > Board Manager, search for ESP32, and install it.

Select the Correct Board and Port:

1. Go to Tools > Board and select ESP32 CAM
2. Then go to Tools > Port and select the port where the ESP32 CAM is connected.

Upload the Code:

1. Load your obstacle detection code (the one using the ultrasonic sensor and ESP32 CAM).
2. Press the upload button to compile and upload the code to the ESP32 CAM.
3. Make sure to make the BOOT connection i.e, connect pin Io0 to Gnd as show in figure below on the ESP32 CAM when the IDE starts uploading the code.

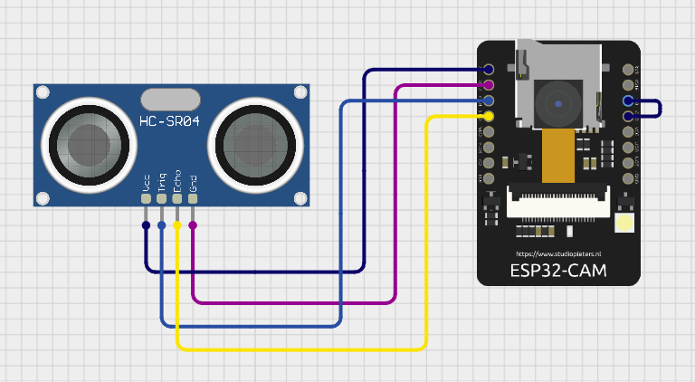
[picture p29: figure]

Figure 25: Ultrasonic sensor wiring diagram for uploading the code

Open the Serial Monitor:

1. Once the code is successfully uploaded, go to Tools > Serial Monitor in the Arduino IDE.
2. Set the baud rate to 115200 at the bottom of the Serial Monitor to match the baud rate in your code.

Observe the Data:

1. As the drone operates, you should see real-time data in the Serial Monitor, such as the distance measured by the ultrasonic sensor.
2. The Serial Monitor will display distance readings in centimetres and print messages when obstacles are detected (e.g., “Obstacle detected! Hovering...”).

5.3 Accessing ESP32 CAM Wi-Fi Access Point

Power on the ESP32 CAM:

1. Connect the 5v and Gnd pins of the ESP32 to appropriate power source. Alternatively, a 3.3 v power supply can also be used.

Connecting to the Wi-Fi

1. Take around 30-60 secs for the ESP32 to turn on the Wi-Fi once powered up
2. On you laptop or any device, navigate to the Wi-Fi settings and select the ESP32cam and enter the network security key = 123456789 . The SSID and security key of the WiFi Access Point can be changed by rebooting the Arduino ino file with the steps provided in step 3.

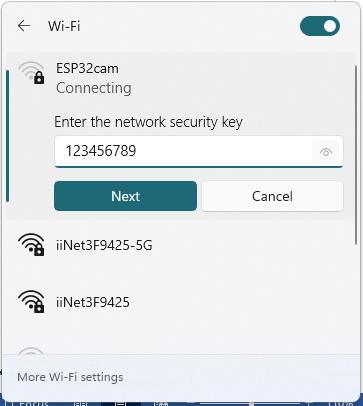
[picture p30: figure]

Figure 26: Wi-Fi connection using ESP32-CAM

3. To modify the SSID and password, just change the characters in green in Arduino IDE.

Figure 27: User id and password

5.3.1 Accessing the video feed

1. Ensure the device is connected to the ESP32’s Wi-Fi access point.
2. Open a web browser on the connected device.
3. Enter the default IP address: 192.168.4.1 and Enter
4. The camera interface should load as displayed below.

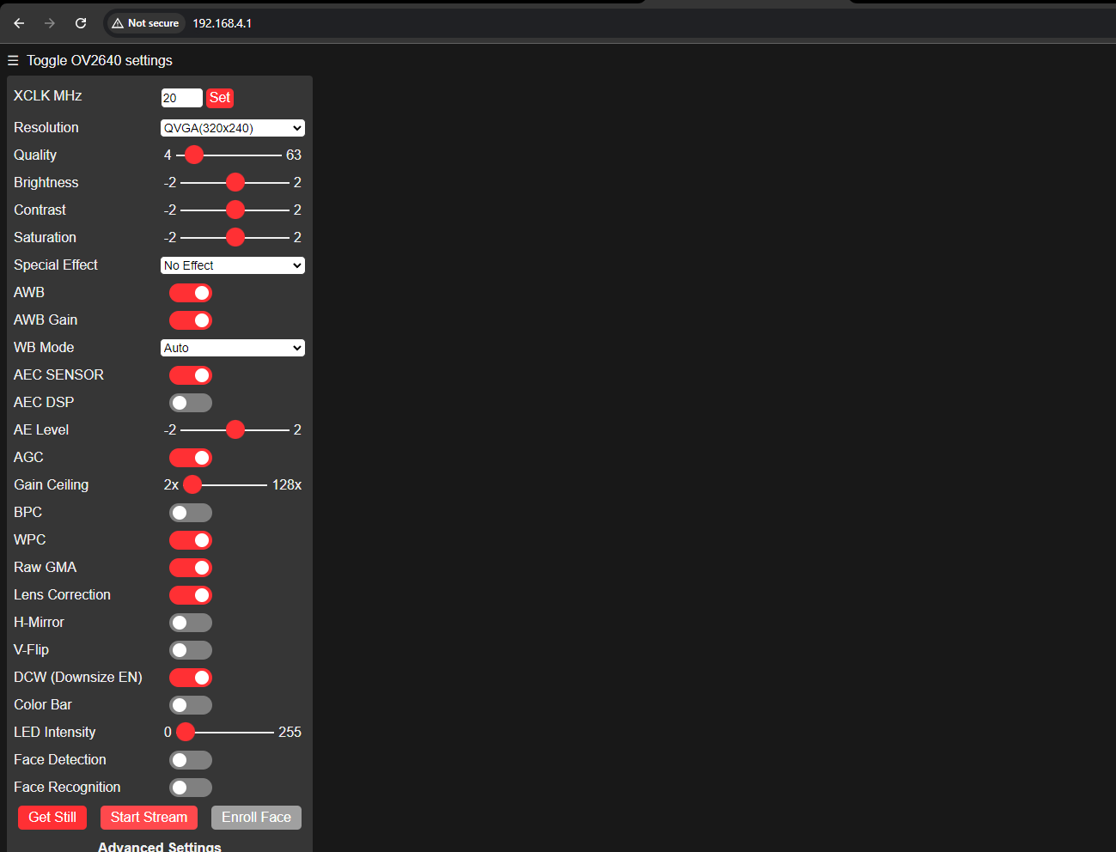
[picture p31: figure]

Figure 28: IP address camera feed

5. Press Start Stream to see the video feed.
6. Also, it should be noted that this IP address can be fed into PyCharm using the OpenCV library to process the feed straightaway.

5.3.2 Connecting external antenna

1. By default, the ESP 32 CAM module utilizes the built in PCB antenna.
2. To connect an external antenna, the resistor on the bottom must be soldered as shown in the figure below

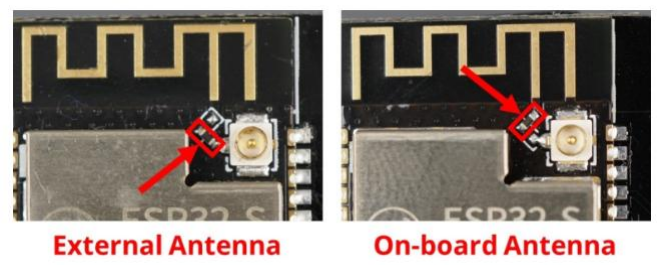
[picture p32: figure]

Figure 29: external and on-board antenna solder connection

3. In the ESP32 CAM module provided along with the drone is soldered for external antenna configuration. So, it can be straight away used by just connecting the UFL connector of the antenna to the ESP32 module.

6 Part 3 – Step-by-Step Instructions Guide

The section provides a step-by-step process to safely operate and fly the drone prototype. Although the designed system failed to achieve a successful flight because the flight controller did not respond to the commands sent through the UART port, the following steps provide a guide for the successful operation if the flight controller is replaced or a new 4 in ESC is purchased, as part of future improvements.

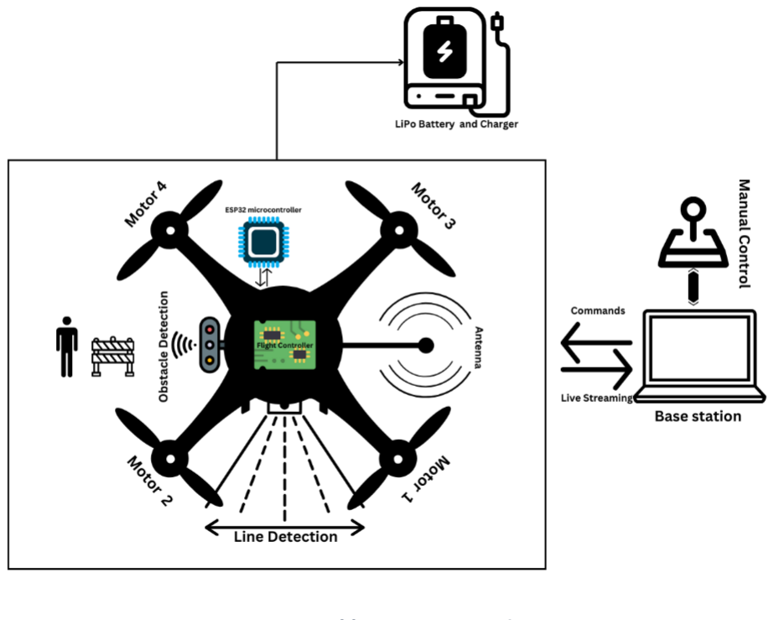
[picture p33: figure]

Figure 30: Basic Design Overview

Step1: Connect the drone to the battery.
- Insert the drone’s battery securely into its designated compartment.

- Ensure the battery is fully charged before use.
- Ensure the Esp32-Cam and the ultrasonic sensor is properly aligned to its respective positions and tightly fixed.

Step2: Place the drone to the Test path
- Position the drone on the floor or corridor where the test will be conducted.
- Ensure the test area is well-lit with a visible line (track) marked on the floor.
- Ensure the area is clear of obstacles for the first few meters of the test path.

Step3: Initialise the Flight
- Activate the drone’s flight mode by pressing the start button. This button acts as an emergency switch for manual shutdown if needed.
- Once the start button is pressed, the drone will power up and take off automatically to a height of 1.2 meters. The drone will hover at this altitude, awaiting navigation instructions.

Step4: Run OpenCV code
- On the laptop, ensure that the OpenCV is properly set up and the line-following code is ready.
- Connect the laptop to the drone via Wi-Fi(ESP32-CAM) module.
- Start running the line following code. This step will ensure the video feed from the drone to your laptop is running for enabling OpenCV to track the line.

Step5: Obstacle Detection and Response
- If an obstacle is detected within 30cm, the drone will automatically hover in place.
- The drone will wait until the obstacle is cleared before resuming navigation.

Step6: Handle T-junctions and intersections for completion of flight
- When the drone encounters a T-junction or an intersection on the path, it will identify it as the end of the test route.
- The drone will stop at the intersection and prepare for a safe landing procedure.

Step7: Safe landing
- Once the drone identifies the T-junction, the landing sequence will begin.
- Ensure the landing area is clear of any obstacles.
- The landing gear helps to achieve a smooth landing.

Step8: Emergency Switch
- In case of communication failure, press the emergency switch for turning to manual control. Here, in the designed prototype, emergency switch is not implemented, and this might lead to control failure during emergency situations.

Step9: Flight Shutdown
- Once the flight is complete, disconnect the battery from the drone to power it down.

7. Conclusion

The comprehensive user guide and manual presented above provides a detailed overview of different components, assembly process and steps required for achieving a successful flight. Each section elaborates on the individual parts of the drone, including mounting peripherals, preparing the system and ensuring proper functionality. However, due to the system integration challenges experienced during the testing phase, it is recommended to consider using a different flight controller or ESC in future iterations to successfully demonstrate the line following functionality. This guide serves as a foundation for further improvements and development of the drone system.

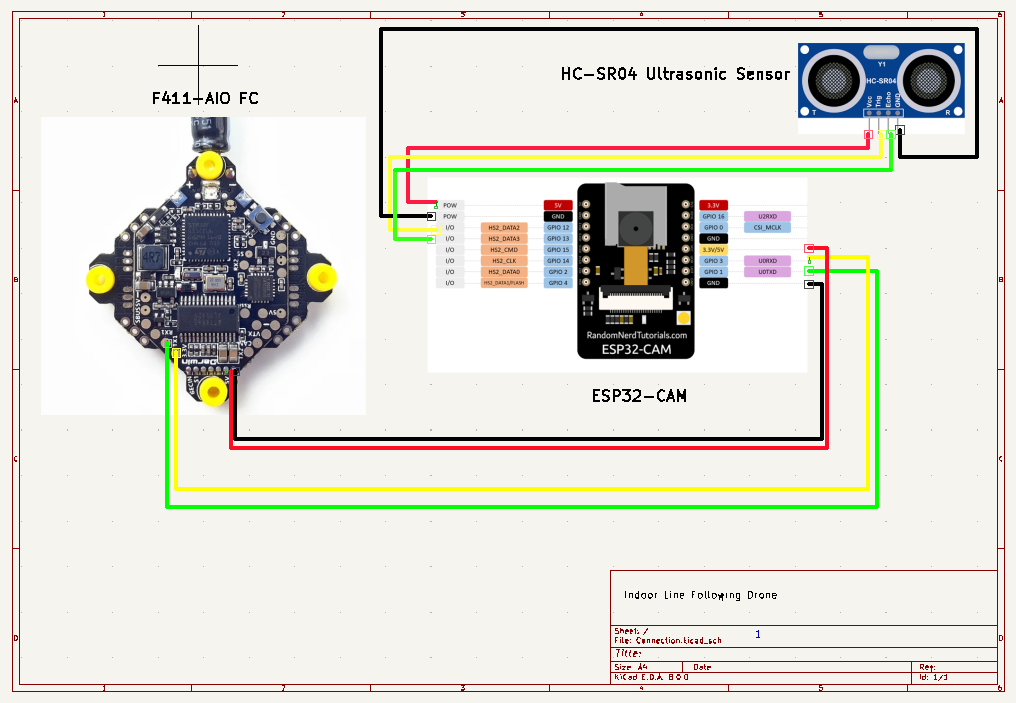
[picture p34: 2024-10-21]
Hardware-diagrams/Wiring Diagram.png

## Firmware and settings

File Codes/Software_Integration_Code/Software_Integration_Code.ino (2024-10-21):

#include "esp_camera.h"
#include <WiFi.h>
#include <WebServer.h>
#include <ArduinoJson.h>
#include <HardwareSerial.h>

// Define the camera model
#define CAMERA_MODEL_AI_THINKER
#include "camera_pins.h"

// Define Wi-Fi credentials
const char *ssid = "ESP32cam";
const char *password = "123456789";

// Ultrasonic Sensor Pins
const int trigPin = 12;  // GPIO pin for Trig
const int echoPin = 13;  // GPIO pin for Echo
int distance_limit = 30; // Distance limit in centimeters for obstacle detection

unsigned long distance_cm = 0;
int object_status = 1; // 0 = detected, 1 = not detected

// Create a web server on port 80
WebServer server(80);

// Initialize UART for communication with flight controller (FC)
HardwareSerial fcSerial(1);  // Use Serial1 for FC communication (TX: GPIO 17, RX: GPIO 16)

// MSP command IDs
#define MSP_SET_RAW_RC 200

// Function to calculate MSP checksum
uint8_t calculateChecksum(uint8_t *data, uint8_t length) {
    uint8_t checksum = 0;
    for (uint8_t i = 0; i < length; i++) {
        checksum ^= data[i];
    }
    return checksum;
}

// Function to send MSP commands to the flight controller
void sendMSPCommand(uint8_t command, uint8_t *payload, uint8_t payloadSize) {
    // MSP message structure
    fcSerial.write('$');
    fcSerial.write('M');
    fcSerial.write('<');
    fcSerial.write(payloadSize);  // Payload size
    fcSerial.write(command);      // Command ID

    // Send the payload
    for (int i = 0; i < payloadSize; i++) {
        fcSerial.write(payload[i]);
    }

    // Calculate and send checksum
    uint8_t checksum = payloadSize ^ command;
    for (int i = 0; i < payloadSize; i++) {
        checksum ^= payload[i];
    }
    fcSerial.write(checksum);
}

// Function to handle incoming POST requests
void handlePost() {
    if (server.hasArg("plain")) {  // Check if there is data in the body
        String body = server.arg("plain");  // Get the body content
        Serial.print("Received body: ");
        Serial.println(body);  // Print received data

        DynamicJsonDocument doc(1024);  // Create a JSON document to parse the incoming data
        DeserializationError error = deserializeJson(doc, body);
        if (error) {
            Serial.println("Failed to parse JSON");
            server.send(400, "application/json", "{\"status\":\"error\",\"message\":\"Invalid JSON\"}");
            return;
        }

        // Extract lr and curve values
        int lr = doc["lr"];
        int curve = doc["curve"];

        Serial.print("Received lr: ");
        Serial.println(lr);
        Serial.print("Received curve: ");
        Serial.println(curve);

        // Check if there's an obstacle
        if (object_status == 0) {
            Serial.println("Obstacle detected. Drone will hover, no commands sent.");
            // If there's an obstacle, stop the drone (send neutral MSP command or hover)
            uint16_t rcData[8] = {1500, 1500, 1500, 1500, 1500, 1500, 1500, 1500};  // Neutral RC values (hover)
            uint8_t payload[16];
            for (int i = 0; i < 8; i++) {
                payload[2 * i] = rcData[i] & 0xFF;
                payload[2 * i + 1] = (rcData[i] >> 8) & 0xFF;
            }
            sendMSPCommand(MSP_SET_RAW_RC, payload, 16);
        } else {
            // If no obstacle, proceed with line-following commands
            uint16_t rcData[8] = {1500, 1500, 1500, 1500, 1500, 1500, 1500, 1500};  // Default RC values (neutral)
            rcData[0] = 1500 + lr;  // Adjust roll (left/right) based on `lr`
            rcData[1] = 1500 + curve;  // Adjust pitch based on `curve`

            // Create MSP payload with raw RC data
            uint8_t payload[16];
            for (int i = 0; i < 8; i++) {
                payload[2 * i] = rcData[i] & 0xFF;
                payload[2 * i + 1] = (rcData[i] >> 8) & 0xFF;
            }

            // Send the MSP command to the flight controller
            sendMSPCommand(MSP_SET_RAW_RC, payload, 16);

            server.send(200, "application/json", "{\"status\":\"success\"}");  // Send success response
        }
    } else {
        Serial.println("No data received in POST request");
        server.send(400, "application/json", "{\"status\":\"error\",\"message\":\"No data received\"}");
    }
}

void startCameraServer();
void setupLedFlash(int pin);
void readUltrasonicSensor();  // Function to read the ultrasonic sensor

// Function to handle the root page request
void handleRoot() {
    // HTML page with camera stream and object detection status
    server.send(200, "text/html",
    "<h1>ESP32 Camera with Ultrasonic Sensor</h1>"
    "<img src='/stream' style='width: 100%; height: auto;'>"
    "<p>Object Status: <span id='status'></span></p>"
    "<script>"
    "setInterval(function() {"
    "  fetch('/readDistance').then(res => res.text()).then(data => {"
    "    document.getElementById('status').innerHTML = data;"
    "  });"
    "}, 1000);"
    "</script>"
    );
}

// Function to handle distance reading
void handleDistance() {
    String status = String(object_status);  // Convert status to a string
    server.send(200, "text/plane", status);  // Send the object status
}

// Function to read distance from the ultrasonic sensor
void readUltrasonicSensor() {
    // Trigger the ultrasonic sensor
    digitalWrite(trigPin, LOW);
    delayMicroseconds(2);
    digitalWrite(trigPin, HIGH);
    delayMicroseconds(10);
    digitalWrite(trigPin, LOW);

    // Measure the echo time in microseconds
    unsigned long duration = pulseIn(echoPin, HIGH);

    // Convert the duration to distance in centimeters
    distance_cm = duration / 58;

    // Print the distance for debugging
    Serial.print("Distance: ");
    Serial.print(distance_cm);
    Serial.println(" cm");
}


// Initialize the camera and WiFi
void setup() {
    Serial.begin(115200);
    Serial.setDebugOutput(true);
    Serial.println();

    // Initialize UART for FC communication
    fcSerial.begin(115200, SERIAL_8N1, 16, 17);  // Serial1, TX (GPIO 17), RX (GPIO 16)

    // Initialize ultrasonic sensor pins
    pinMode(trigPin, OUTPUT);
    pinMode(echoPin, INPUT);

    // Camera configuration
    camera_config_t config;
    config.ledc_channel = LEDC_CHANNEL_0;
    config.ledc_timer = LEDC_TIMER_0;
    config.pin_d0 = Y2_GPIO_NUM;
    config.pin_d1 = Y3_GPIO_NUM;
    config.pin_d2 = Y4_GPIO_NUM;
    config.pin_d3 = Y5_GPIO_NUM;
    config.pin_d4 = Y6_GPIO_NUM;
    config.pin_d5 = Y7_GPIO_NUM;
    config.pin_d6 = Y8_GPIO_NUM;
    config.pin_d7 = Y9_GPIO_NUM;
    config.pin_xclk = XCLK_GPIO_NUM;
    config.pin_pclk = PCLK_GPIO_NUM;
    config.pin_vsync = VSYNC_GPIO_NUM;
    config.pin_href = HREF_GPIO_NUM;
    config.pin_sccb_sda = SIOD_GPIO_NUM;
    config.pin_sccb_scl = SIOC_GPIO_NUM;
    config.pin_pwdn = PWDN_GPIO_NUM;
    config.pin_reset = RESET_GPIO_NUM;
    config.xclk_freq_hz = 20000000;
    config.frame_size = FRAMESIZE_UXGA;
    config.pixel_format = PIXFORMAT_JPEG;  // for streaming
    config.grab_mode = CAMERA_GRAB_WHEN_EMPTY;
    config.fb_location = CAMERA_FB_IN_PSRAM;
    config.jpeg_quality = 12;
    config.fb_count = 1;

    // Initialize the camera
    esp_err_t err = esp_camera_init(&config);
    if (err != ESP_OK) {
        Serial.printf("Camera init failed with error 0x%x", err);
        return;
    }

    WiFi.softAP(ssid, password);  // Start WiFi Access Point

    startCameraServer();  // Start the camera server

    Serial.print("Camera Ready! Use 'http://");
    Serial.print(WiFi.localIP());
    Serial.println("' to connect");

    // Define the POST route for receiving commands
    server.on("/commands", HTTP_POST, handlePost);
    server.begin();  // Start the server
    Serial.println("Server started and listening for commands");
}

void loop() {
    // Check for obstacles
    readUltrasonicSensor();

    // If the obstacle is detected within the limit, stop all actions
    if (distance_cm <= distance_limit) {
        object_status = 0;  // Object detected
        Serial.println("Obstacle detected! Hovering...");

        // Stay in hover state and keep checking until the obstacle is removed
        while (distance_cm <= distance_limit) {
            readUltrasonicSensor();
            delay(1000);  // Check again after 1 seconds
        }
    }
}

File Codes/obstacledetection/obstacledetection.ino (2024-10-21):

#include "esp_camera.h"
#include <WiFi.h>
#include <WebServer.h>
 
//
// WARNING!!! PSRAM IC required for UXGA resolution and high JPEG quality
//            Ensure ESP32 Wrover Module or other board with PSRAM is selected
//            Partial images will be transmitted if image exceeds buffer size
//
//            You must select partition scheme from the board menu that has at least 3MB APP space.
//            Face Recognition is DISABLED for ESP32 and ESP32-S2, because it takes up from 15
//            seconds to process single frame. Face Detection is ENABLED if PSRAM is enabled as well
 
// ===================
// Select camera model
// ===================
//#define CAMERA_MODEL_WROVER_KIT // Has PSRAM
//#define CAMERA_MODEL_ESP_EYE  // Has PSRAM
//#define CAMERA_MODEL_ESP32S3_EYE // Has PSRAM
//#define CAMERA_MODEL_M5STACK_PSRAM // Has PSRAM
//#define CAMERA_MODEL_M5STACK_V2_PSRAM // M5Camera version B Has PSRAM
//#define CAMERA_MODEL_M5STACK_WIDE // Has PSRAM
//#define CAMERA_MODEL_M5STACK_ESP32CAM // No PSRAM
//#define CAMERA_MODEL_M5STACK_UNITCAM // No PSRAM
//#define CAMERA_MODEL_M5STACK_CAMS3_UNIT  // Has PSRAM
#define CAMERA_MODEL_AI_THINKER // Has PSRAM
//#define CAMERA_MODEL_TTGO_T_JOURNAL // No PSRAM
//#define CAMERA_MODEL_XIAO_ESP32S3 // Has PSRAM
// ** Espressif Internal Boards **
//#define CAMERA_MODEL_ESP32_CAM_BOARD
//#define CAMERA_MODEL_ESP32S2_CAM_BOARD
//#define CAMERA_MODEL_ESP32S3_CAM_LCD
//#define CAMERA_MODEL_DFRobot_FireBeetle2_ESP32S3 // Has PSRAM
//#define CAMERA_MODEL_DFRobot_Romeo_ESP32S3 // Has PSRAM
#include "camera_pins.h"
 
// ===========================
// Enter your WiFi credentials
// ===========================
const char *ssid = "ESP32cam";
const char *password = "123456789";
 
// Ultrasonic Sensor Pins
const int trigPin = 12;  // GPIO pin for Trig
const int echoPin = 13;  // GPIO pin for Echo
int distance_limit = 30; // Distance limit in inches for obstacle detection
 
unsigned long distance_cm = 0;
int object_status = 1; //0= detected, 1= not detected
//Web Server initialisation on port 80
 
WebServer server(80);
 
 
void startCameraServer();
void setupLedFlash(int pin);
void readUltrasonicSensor();  // Function to read the ultrasonic sensor
 
//Function to handle the root page request
void handleRoot() {
  // HTML page with camera stream and object detection status
  server.send(200, "text/html",
    "<h1>ESP32 Camera with Ultrasonic Sensor</h1>"
    "<img src='/stream' style='width: 100%; height: auto;'>"
    "<p>Object Status: <span id='status'></span></p>"
    "<script>"
    "setInterval(function() {"
    "  fetch('/readDistance').then(res => res.text()).then(data => {"
    "    document.getElementById('status').innerHTML = data;"
    "  });"
    "}, 1000);"
    "</script>"
  );
}
 
// Function to handle distance reading
void handleDistance() {
  String status = String(object_status);  // Convert status to a string
  server.send(200, "text/plane", status);  // Send the object status
}
 
void setup() {
  Serial.begin(115200);
  Serial.setDebugOutput(true);
  Serial.println();
 
  // Initialize ultrasonic sensor pins
  pinMode(trigPin, OUTPUT);
  pinMode(echoPin, INPUT);
 
  camera_config_t config;
  config.ledc_channel = LEDC_CHANNEL_0;
  config.ledc_timer = LEDC_TIMER_0;
  config.pin_d0 = Y2_GPIO_NUM;
  config.pin_d1 = Y3_GPIO_NUM;
  config.pin_d2 = Y4_GPIO_NUM;
  config.pin_d3 = Y5_GPIO_NUM;
  config.pin_d4 = Y6_GPIO_NUM;
  config.pin_d5 = Y7_GPIO_NUM;
  config.pin_d6 = Y8_GPIO_NUM;
  config.pin_d7 = Y9_GPIO_NUM;
  config.pin_xclk = XCLK_GPIO_NUM;
  config.pin_pclk = PCLK_GPIO_NUM;
  config.pin_vsync = VSYNC_GPIO_NUM;
  config.pin_href = HREF_GPIO_NUM;
  config.pin_sccb_sda = SIOD_GPIO_NUM;
  config.pin_sccb_scl = SIOC_GPIO_NUM;
  config.pin_pwdn = PWDN_GPIO_NUM;
  config.pin_reset = RESET_GPIO_NUM;
  config.xclk_freq_hz = 20000000;
  config.frame_size = FRAMESIZE_UXGA;
  config.pixel_format = PIXFORMAT_JPEG;  // for streaming
  //config.pixel_format = PIXFORMAT_RGB565; // for face detection/recognition
  config.grab_mode = CAMERA_GRAB_WHEN_EMPTY;
  config.fb_location = CAMERA_FB_IN_PSRAM;
  config.jpeg_quality = 12;
  config.fb_count = 1;
 
  // if PSRAM IC present, init with UXGA resolution and higher JPEG quality
  //                      for larger pre-allocated frame buffer.
  if (config.pixel_format == PIXFORMAT_JPEG) {
    if (psramFound()) {
      config.jpeg_quality = 10;
      config.fb_count = 2;
      config.grab_mode = CAMERA_GRAB_LATEST;
    } else {
      // Limit the frame size when PSRAM is not available
      config.frame_size = FRAMESIZE_SVGA;
      config.fb_location = CAMERA_FB_IN_DRAM;
    }
  } else {
    // Best option for face detection/recognition
    config.frame_size = FRAMESIZE_240X240;
#if CONFIG_IDF_TARGET_ESP32S3
    config.fb_count = 2;
#endif
  }
 
#if defined(CAMERA_MODEL_ESP_EYE)
  pinMode(13, INPUT_PULLUP);
  pinMode(14, INPUT_PULLUP);
#endif
 
  // camera init
  esp_err_t err = esp_camera_init(&config);
  if (err != ESP_OK) {
    Serial.printf("Camera init failed with error 0x%x", err);
    return;
  }
 
  sensor_t *s = esp_camera_sensor_get();
  // initial sensors are flipped vertically and colors are a bit saturated
  if (s->id.PID == OV3660_PID) {
    s->set_vflip(s, 1);        // flip it back
    s->set_brightness(s, 1);   // up the brightness just a bit
    s->set_saturation(s, -2);  // lower the saturation
  }
  // drop down frame size for higher initial frame rate
  if (config.pixel_format == PIXFORMAT_JPEG) {
    s->set_framesize(s, FRAMESIZE_QVGA);
  }
 
#if defined(CAMERA_MODEL_M5STACK_WIDE) || defined(CAMERA_MODEL_M5STACK_ESP32CAM)
  s->set_vflip(s, 1);
  s->set_hmirror(s, 1);
#endif
 
#if defined(CAMERA_MODEL_ESP32S3_EYE)
  s->set_vflip(s, 1);
#endif
 
// Setup LED FLash if LED pin is defined in camera_pins.h
#if defined(LED_GPIO_NUM)
  setupLedFlash(LED_GPIO_NUM);
#endif
 
 WiFi.softAP(ssid, password);
 WiFi.setSleep(false);
 
 // Start the camera server
  startCameraServer();
 
  // Start the web server
  server.on("/", handleRoot);  // Serve the main HTML page
  server.on("/readDistance", handleDistance);  // Serve the distance data
  server.begin();  // Start the web server
 
  Serial.print("Camera Ready! Use 'http://");
  Serial.print(WiFi.localIP());
  Serial.println("' to connect");
}
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
